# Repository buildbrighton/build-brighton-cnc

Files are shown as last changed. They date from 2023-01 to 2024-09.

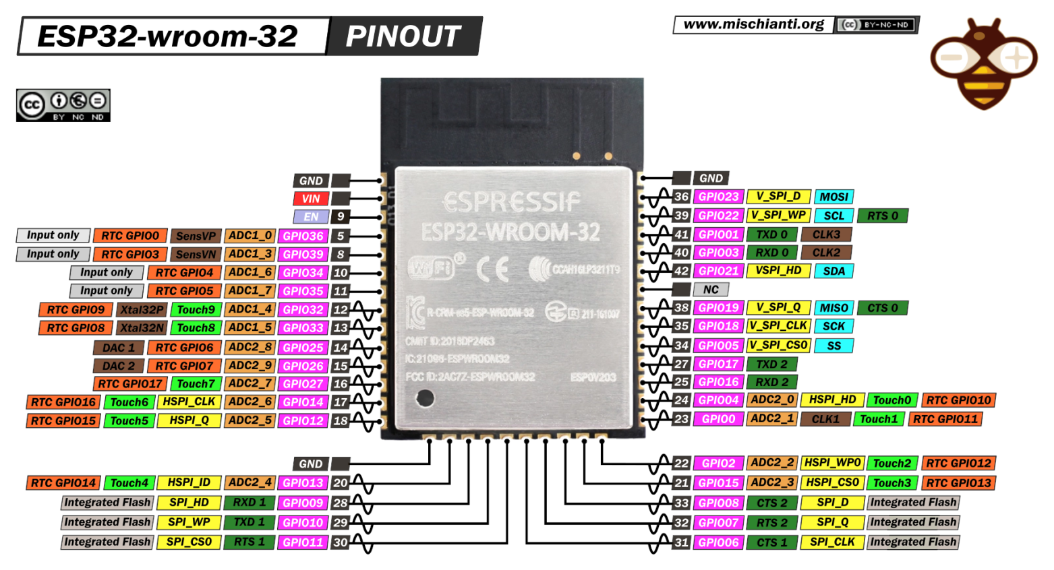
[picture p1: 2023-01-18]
images/ESP32-wroom-32-pinout-mischianti-high-resolution.png

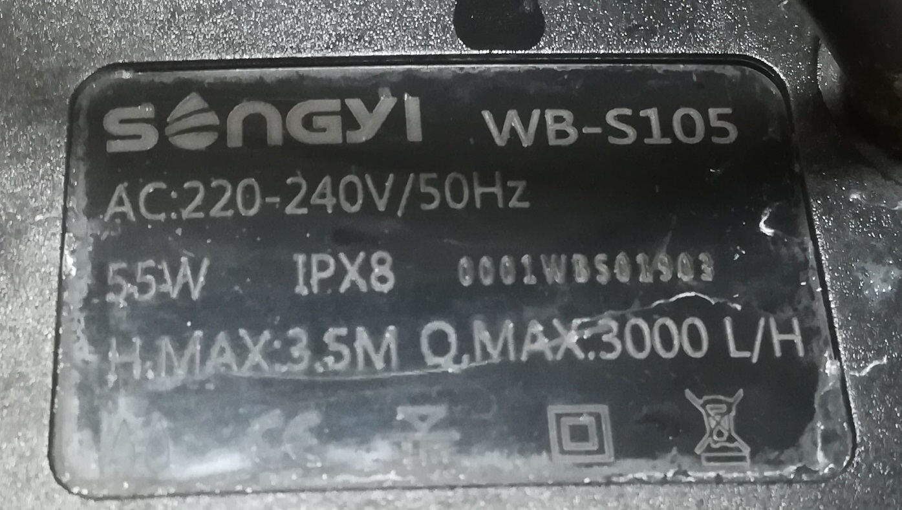
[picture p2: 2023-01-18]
images/water_pump_name_plate.jpg

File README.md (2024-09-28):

# build-brighton-cnc

A repository of code and information about the CNC machine at Build Brighton

You must be inducted to use this machine.

## Machine Description

#### Type

The machine is an ISEL 4433 with a FluidNC controller and a water cooled spindle.

#### Size

The maximum coordinate volume of the machine is 440 x 330 x 160 mm.
The water cooled spindle collides with the door, so the maximum usable depth is 430 mm
The bed is about 300 mm wide.
The X axis is +ve from left to right, Y axis is +ve from front to back, and Z axis is -ve from top to bottom.

#### Spindle

The spindle is rated at 2.2kW and has a speed range of 250 - 24000 rpm.
Speed is controlled by the control board via pwm, start and reverse signals.

#### Spindle Coolant

Coolant for the spindle is stored in a tank under the machine. The pump is located inside the tank. The coolant is tap water and dettol floor cleaner.

#### Control

The control board is an MKS-ESP32. Connection to the controller is either by direct USB or wifi. A PC is setup for use with the machine. It can be controlled directly from a phone or tablet, but the PC is recommended. The PC is dual boot Windows 7 or Ubuntu 16.04 LTS, both of which are out of date and should be upgraded. The PC only has 2GB of ram, which is barely adequate.

## Usage

***DO NOT RUN THE MACHINE WITH THE DOOR OPEN*** Or you will damage yourself.

***DO NOT CUT DIRECTLY ON THE BED*** Or you will damage the bed.

***DO NOT CUT STEEL*** Or you may damage the bearings, ballscrews etc.

***DO NOT DROP TOOLS*** The cutting edges will be damaged and it won't cut well, or at all.

***TOOLS ARE SHARP*** They will slice your skin if handled without care.

***USE A VACUUM IF CUTTING WOOD*** Prefereably, don't cut wood. Use the Carvey for that.

#### Setting up

1. Remove any boxes, equipment or material stored in the machine cabinet. Ensure nothing will get in the way of the moving parts. Don't leave anything in there you down want covered in chips and cutting fluid.

2. Check spindle cooland level and condition. Top up or clean out and replace as required. The level must be at least above the pump, but no more than about 60% full. Make sure the return hose is pointing into the tank and that the tank is covered.

3. Connect the machine, PC, monitor to a power extension cable. Be sure not to cause a trip hazard.

4. Turn on the PC and boot into Linux or Windows. Windows is recommended for now.

5. Connect the water pump to power and check for steady flow of coolant from the return hose.

6. If air cooling is required (recommended), follow procedure for turning on the compressor and run the hose to the air connector on the left front leg.

7. Turn on the machine using the power switch on the right hand side. Release the Emergency Stop button.

8. Connect to the controller. On Windows, this can be done over USB using GRBLPlotter. However, GRBLPlotter is not fully compatible with FluidNC. Alternatively any terminal emulator can connect for a text only interface. FluidNC's web interface is not set up for DNS and itsip address is dynamically allocated, so it must be found using a tool such as Ning (Android) to list all ips on the the network and connecting to each one until the web interface appears. Make sure to connect with `http://` and not `https://`. If anyone knows how to setup a static ip address or configure the DNS, please do.

9. Home all axes using the 'Home All' button next to the jog control, or enter the command `$H`. The machine should gently move into the top left rear corner and back off, one axis at a time.

#### Running a program

1. Upload your gcode to the control board via the web interface. Use a folder with your name to store your files. Alternatively load into GRBLPlotter, etc.

2. Affix you stock material to the bed. For thin sheet material, place a sacrificial block of material under your stock to protect the machine bed. NEVER CUT DIRECTLY ON THE BED. Bar clamps can be used to hold the stock and sacrifical layer to the bed. Bar clamps must have roughly equal height material on both sides of the bolt to function correctly. For thicker and smaller peices, use the clamp/support blocks fixed to the near left corner. The cam grip should be on the right hand side so that its clamping force does not cause it to slide along the T slot. Use shim blocks if the stock doesnt reach the clamp. Make sure that your stock has enough clearance at the edges so as not to cut into the blocks.

3. Change the tool. 
     1. Press the white button on the left hand side. The machine will move the spindle over the tool height probe.
     2. Open the door and use an 18 and 22 mm spanner to remove the collet nut.
     3. Replace the collet with the correct size for your tool. The tool can be up to approx 10% smaller than the collet size and still work.
     4. Insert the collet into the nut *first*, then insert the tool, making sure that the shank of the tool reaches the rear of the collet's gipping surface.
     5. Thread the nut back on to the spindle until finger tight. Use the spanners with *reasonable* force to securely tighten the nut.
     6. **Close the door** and press the *'Start'* button. The machine will move down until the tool touches the tool height probe.
     7. Read the second tool probe Z position. Subtract from 150. Enter the command `G43.1.Z{result}` replacing `{result}` with the value just calcuated. eg, probe return -124.5, value entered is 150 - 124.5 = 25.5
     8. Validate the tool height offset with the command `$#` and check that TLO matches the value entered.

4. Locate the stock. This can be done by eye, or by gently jogging the tool (with the spindle running) into the stock untill it starts cutting. There is also a set of wigglers in the red toolchest in the metal shop that can do the same without cutting into the stock, and is potentially more accurate. Wigglers require an extra tool change. Generally, either the top centre or top near left corner are used for location.

5. Select and zero the work coordinate offset with the commands `G54` and `G92 X0 Y0 Z0`. Each axis can be zeroed independantly after locating for convenience, eg `G92 X0`.

6. If required, open the door and apply cutting fluid to the stock and tool. **Close the door** when done.

6. Press the play button next to your gcode in the web interface, or start sending gcode if using GRBLPlotter or similar.

7. Observe the machine. Do not let it run unattended. You will almost certainly need to adjust feeds and speeds with the override controls, make sure chips are clearing correctly, and that generally everything is ok. The machine should sing with good settings. Bad settings will make it sound like a wood chipper.

8. Press the red *'Stop'* button at any time to hold the program. Press the green *'Start'* button to resume. To stop the program completely use the stop button in the web interface or gcode sender. In an **emergency**, use the *emergency stop* button on the right hand side near the power switch.

9. Your gcode should include a `G28` command at the end to return the machine to the home position. If you stop for any other reason, enter the command `G28` to move the machine back to home and out of the way.

10. When using multiple tools, save each tool operation as a seperate g-code. Repeat steps 3 and 6 through 9 for each tool. When using multiple setups (eg, flipping the stock upside-down, or setting it on its side) repeats steps 2 and  4 through 9 for each setup.

#### Finishing

1. Remove the tool from the collet. Clean chips and cutting fluid from the tool. Put the tool safely back in its protective packaging and return it neatly to where it belongs.

2. Ensure the machine has returned home with `G28`, that the spindle is stopped with `M5`, and that air cooling is turned off with `M9`.

3. Unclamp your work and remove it and any fixturing, like a sacrificial board or clamp shim blocks.

4. Clean out ***all*** the chips, cleanup any cutting fluid and degrease.

5. Turn off the pump, the machine and this PC.

6. Stash whatever machine related things you pulled out of the enclosure back inside and close the door.

7. Carefully roll up the power extension cable and return it.

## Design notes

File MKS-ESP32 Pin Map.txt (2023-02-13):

ESP32 gpio map for MKS-DLC32, plus Expander Board v0.9

GPIO No.	MKS Net			Other			MKS Port	EXP Board	Function
gpio.0		I2C_SDA			BOOTMODE		EXP2.4		SW4			MACRO
gpio.1		TXD				USB
gpio.2		IO2				Blue LED
gpio.3		RXD				USB
gpio.4		I2C_SCL							EXP2.5		SW5			DOOR/INTERLOCK 
gpio.5		LCD_EN							EXP1.3		OC3			FORWARD
gpio.6		Unusable		CLK
gpio.7		Unusable		SD0
gpio.8		Unusable		SD1
gpio.9		Unusable		SD2
gpio.10		Unusable		SD3
gpio.11		Unusable		CMD
gpio.12		SD_DO
gpio.13		SD_DI
gpio.14		SD_SCK
gpio.15		SD_CS
gpio.16		I2S_BCK
gpio.17		I2S_WS
gpio.18		LCD_SCK							EXP2.2		SW2			CYCLE START
gpio.19		LCD_MISO						EXP2.1		SW3			FEED_HOLD
gpio.20		n/c
gpio.21		I2S_DATA
gpio.22		PROBE							J12						PROBE
gpio.23		LCD_MOSI						EXP2.6		SW1			RESET/ESTOP
gpio.24		n/c
gpio.25		LCD_CS							EXP1.7		OC1			PWM/SPEED
gpio.26		LCD_TOUCH_CS					EXP1.5		OC2			REVERSE
gpio.27		LCD_RST							EXP1.4		OC4			FLOOD/AIR
gpio.28		n/c
gpio.29		n/c
gpio.30		n/c
gpio.31		n/c
gpio.32		LC								J7			OC6			AUX1
gpio.33		LCD_RS							EXP1.8		OC5			MIST
gpio.34		Z-								J11						LIMIT_Z
gpio.35		Y-								J10						LIMIT_Y
gpio.36		X-				SENSOR_VP		J9						LIMIT_X
gpio.37		n/c
gpio.38		n/c
gpio.39		SD_DET(n/a)		SENSOR_VN

i2so.0		#STEP_ENABLE
i2so.1		X_STEP
i2so.2		X_DIR
i2so.3		Z_STEP
i2so.4		Z_DIR
i2so.5		Y_STEP
i2so.6		Y_DIR
i2so.7		BEEPER							J4			OC7			AUX2

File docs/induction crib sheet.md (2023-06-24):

### Isel CNC induction crib sheet (draft)

- Main Power - plug, switch, estop
- Cooling pump - power plug, water level, flow rate
- Connectivity - fluidNC, ning, wifi, pc via serial port, gcode senders, GRBL Plot
- Web gui - axis DROs, homing the machine, jog joystick, speed and feed overrides, message window, reseting and clearing faults, command line, supported gcode, running gcode from SD card
- Endstops - no software endstops, pulling the machine off the stops
- Start and Stop physical buttons - stop is feed hold, start is resume
- Changing tools - tool change macro, ER collet operation, height probe
- Available tools, tool wear and breakage
- Spindle behaviour - torque curve, motor heat source
- Feeds and speeds - tool material and diameter, chip loading, deflection, material properties, heat removal
- Clamping work to the bed, sacrificial material, blocks and clamps
- Work coordinate offsets G54-G59
- Door safety - do not run with the door open,
- Cleaning up afterwards - dust, swarf, cutting fluid

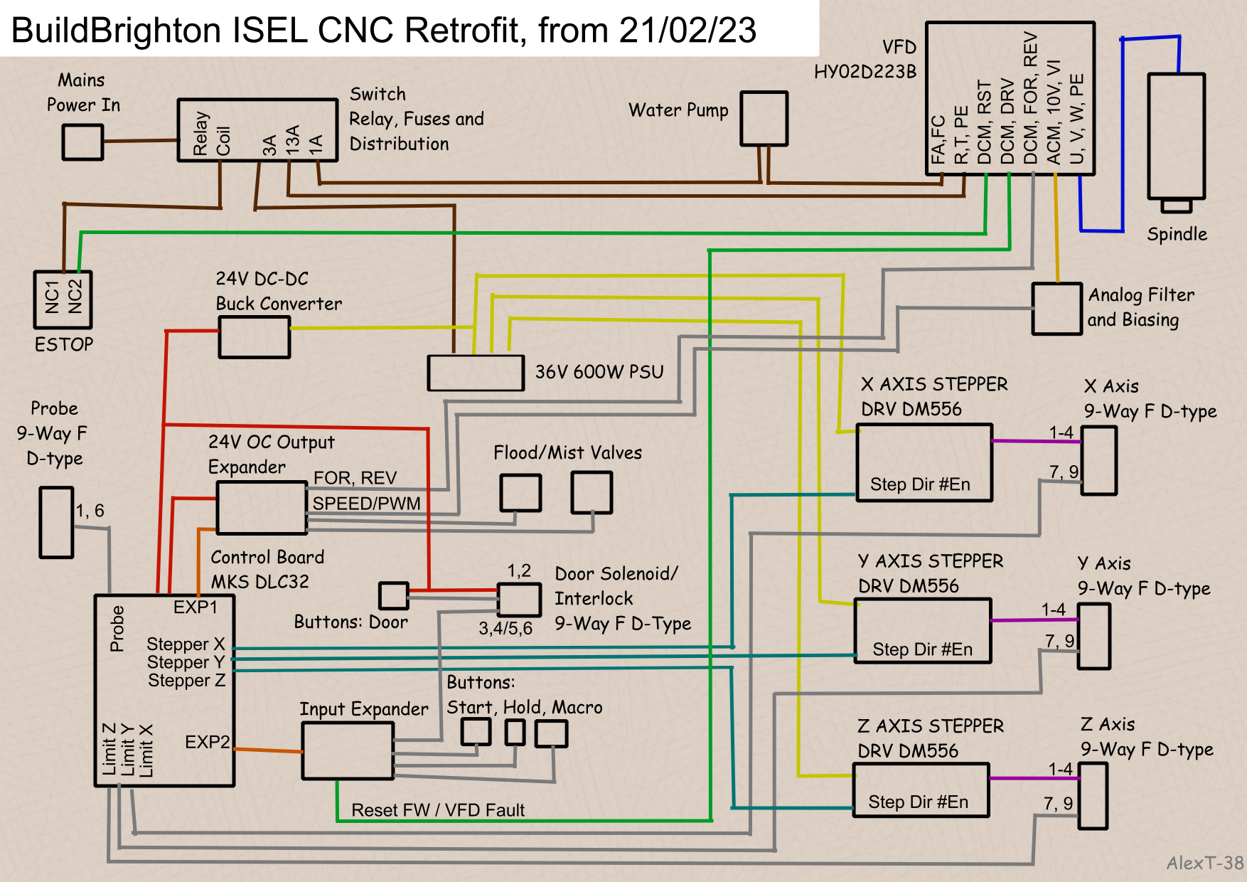
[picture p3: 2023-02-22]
images/refit_schematic_overview.png

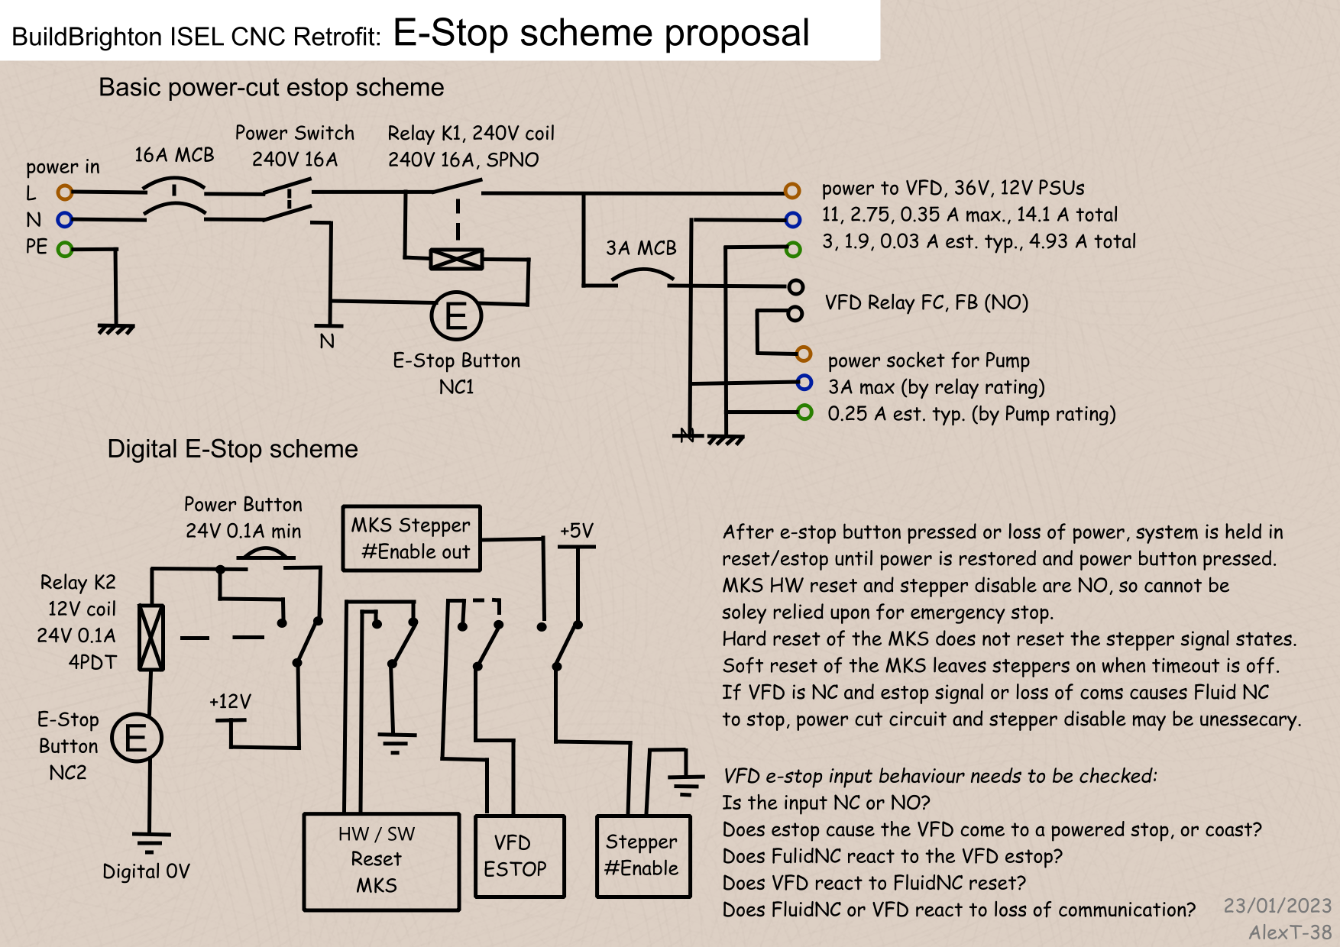
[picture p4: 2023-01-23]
images/cnc_estop_schemes.png

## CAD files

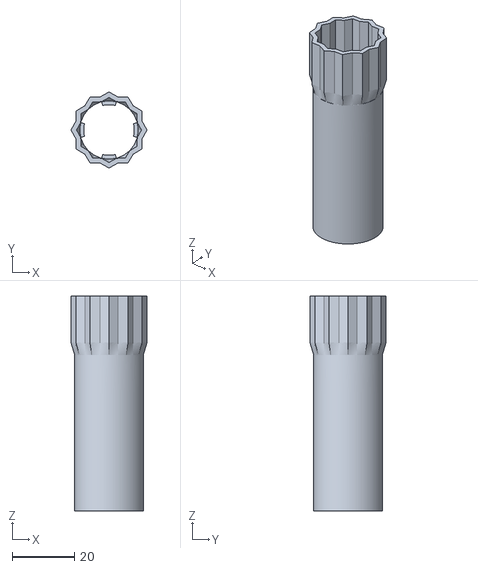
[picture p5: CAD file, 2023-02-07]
hardware/accessories/EAO Series 31 Push Button Accessories v1.stl
24.4 x 24.4 x 69.0

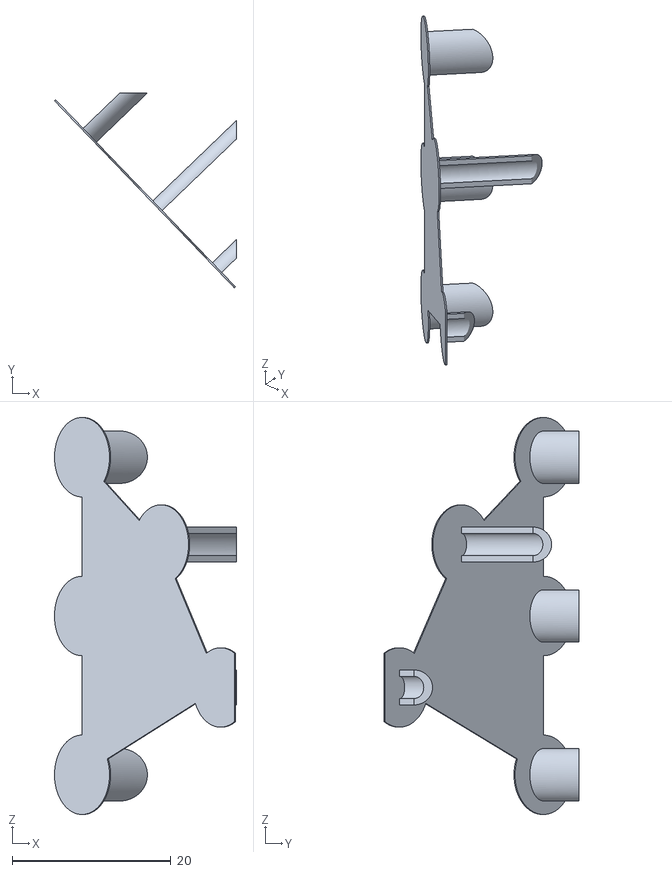
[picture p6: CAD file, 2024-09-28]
hardware/models/Valve Bracket supports.stl
22.9 x 24.5 x 50.0

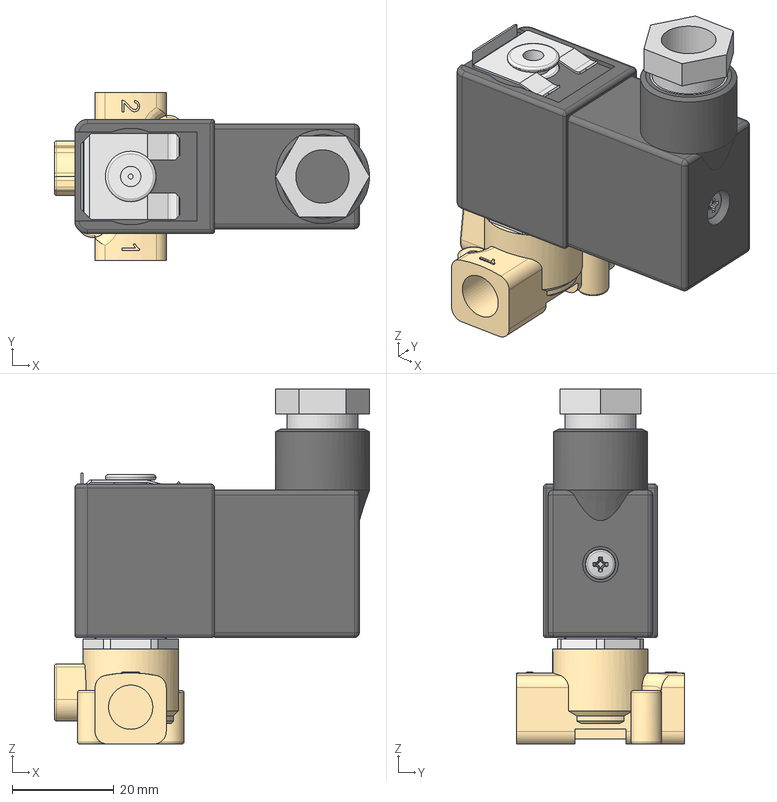
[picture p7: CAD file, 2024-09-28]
hardware/models/ASGO-G356A001.step
62.0 x 33.0 x 69.8 mm
Connector
Solenoid
Valve Body
92005A132_NO THREADS_Steel Pan Head Phillips Screw

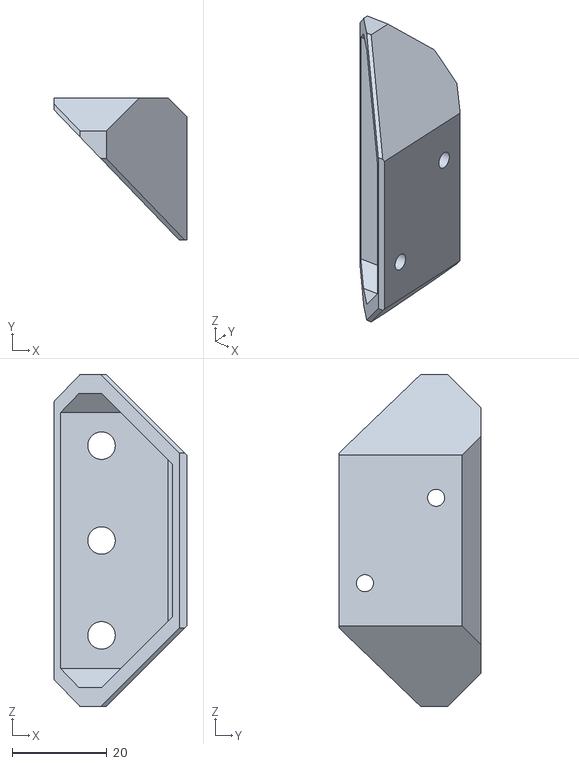
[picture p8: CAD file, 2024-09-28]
hardware/models/Valve Bracket.stl
28.0 x 30.0 x 70.0

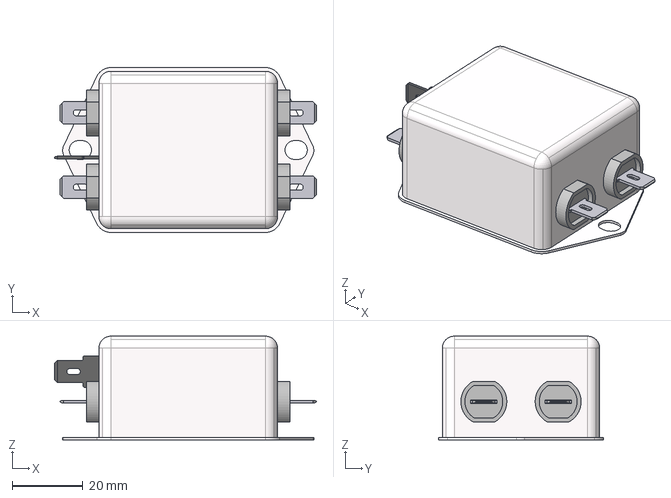
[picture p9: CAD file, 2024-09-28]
hardware/models/fn2060-6-06.stp
74.0 x 46.6 x 29.3 mm

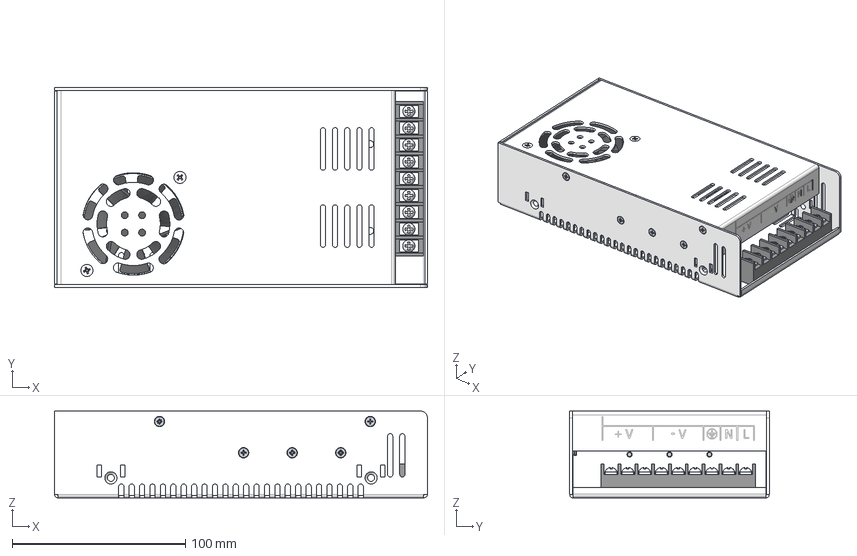
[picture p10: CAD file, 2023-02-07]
hardware/models/Pulse_power_supply_36V_600W.stp
215.0 x 115.0 x 50.0 mm
Основание ИИП
Крышка ИИП
ISO 7046-1 - M3 x 4Z x 12
Кулер 60 х 60
Шайба 4х4х1.3 x 9
Винт M4x6 с полукруглой головкой x 9
Винт М4х12 x 2

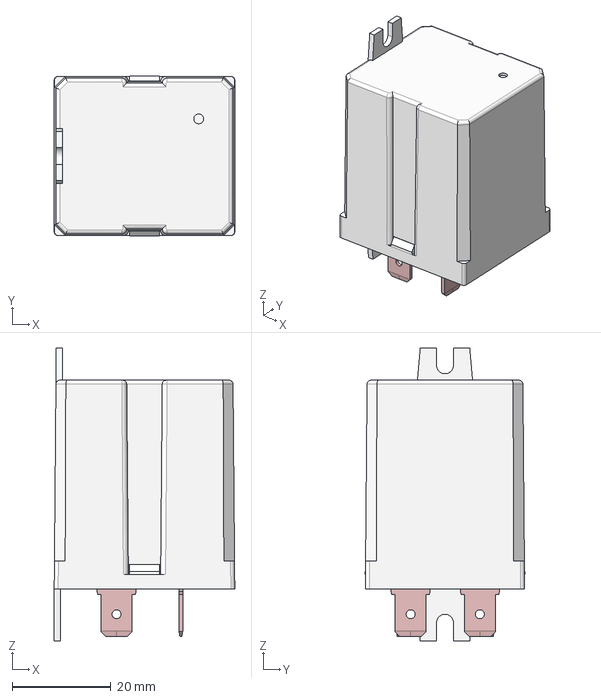
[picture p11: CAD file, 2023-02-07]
hardware/models/6531xxxx0300.stp
36.5 x 32.3 x 59.2 mm

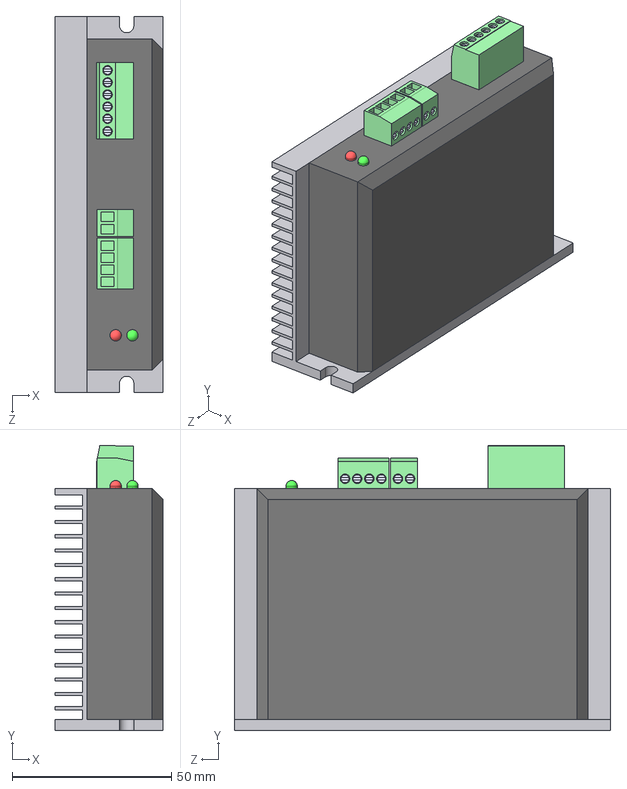
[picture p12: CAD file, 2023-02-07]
hardware/models/Lead Shine DM556.STEP
34.0 x 89.5 x 118.0 mm

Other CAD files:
fusion360/FluidNC Refit Machine Model.f3d

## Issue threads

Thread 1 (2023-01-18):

VFD electrical installation issues.

AlexT-38, 2023-01-18:
Power input cable undersized and wrong type (appears to be 5A 2 core).
Protective Earth not connected to spindle or mains power input.
Spindle loom has PE, but is not connected at the VFD.

Action to take:
1) replace mains power input cable with 3 core flex with current rating >=10A
2) connect VFD PE to spindle loom PE at terminal block below VFD.

AlexT-38, 2023-01-21:
Flex has been upgraded.
Spindle loom and VFD bonded to protective earth.
Will close this issue once the installation has been checked and tested.

Closed 2023-02-10.

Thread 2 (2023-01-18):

VFD is missing opto-isolators for digital outputs

AlexT-38, 2023-01-18:
The VFD's configurable open-collector outputs UPD and DRV do not work because their opto-isolators have not been fitted to its control board.
This is a known issue with Huanyang VFDs since at least 2014.
If these outputs are required, the missing parts can be purchased and soldered onto the board relatively easily.
see: https://www.youtube.com/watch?v=cSjaUhPZzqM

AlexT-38, 2023-02-10:
As we are using FOR/REV/PWM control going forward, we should fit these missing components so that we can use the relay for the cooling pump and the digital OC outputs to signal faults to the controller.

AlexT-38, 2023-02-10:
Parts ordered.

AlexT-38, 2023-03-06:
Fitted and working.

Closed 2023-03-06.

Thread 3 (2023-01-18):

Water pump hose barb is wrong size

AlexT-38, 2023-01-18:
The water pump output has an M20x1.75F thread.
The hose is 10/8mm (OD/ID)
The hose barb thread measures as M19.5x1.5, and fits 5/8" (15.9mm) hoses.
Currently the hose is wedged into the hose barb ID using electrical tape to pad the hose out to 12mm.
The threads catch just enough to stop the barb from simply falling out.

M20x1.75M threaded hose barbs do not appear to exist.
Nor is there any sign of a supplier of accessories for this brand of pump.

A suitable hose barb will have to be printed, or machined if a print isn't up to the job.

Closed 2023-02-10.

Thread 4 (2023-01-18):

VFD Aux Pump does not start.

AlexT-38, 2023-01-18:
The VFD's relay output does not operate when configured as the aux pump output.

With the following parameters set (where non-default),

PD130: 1 - no. of aux pumps
PD052: 25 - output F: aux pump 1

relay is expected to operate on run-start and release 20s after run-stop.

Relay output confirmed working by setting:

PD052: 01 - output F: in run

This setting stops the pumps as soon as the motor has stopped, which in practice is probably sufficient.

AlexT-38, 2023-02-10:
PD135 controls the minimum motor drive voltage below which the pump will stop running (after PD136 seconds).
The default is 95%, which is probably why this wasn't working.

PD138 and 139 appear to provide similar limits based on spindle frequency. However the manual is as clear as muck on the matter, and refers only to "sleep time" for these parameters and PD137, rather than "pump sleep time" for PD135 and PD136.

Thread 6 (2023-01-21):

Spindle collides with door.

AlexT-38, 2023-01-21:
Spindle (specifically the mount) collides with the front panel of the door when the gantry is on the -Y limit switch.
Y-homing is currently configured to use the +Y limit switch.
The -Y limit switch position can be adjusted by loosening the mounting screws and sliding it.
Slack in the wire loom may be the limiting factor on switch placement.

AlexT-38, 2023-03-06:
Not fixed yet, but moved G28 to back left instead of front left (this is also where it homes to). Fusion360 uses G28 to park the machine after completion.

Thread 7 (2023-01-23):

E-Stop implementation

AlexT-38, 2023-01-23:
See [FluidNC E-Stop docs](https://github.com/bdring/FluidNC/wiki/E-Stop-Button) and [onefinitycnc forum post](https://forum.onefinitycnc.com/t/best-way-to-e-stop-spindle-and-vfd/10792).

#### E-Stop requirements
We need to ensure that the machine can be safely stopped in an emergency. This includes machine faults, as well as direct risk to life events.
The method used should fail safe. That is, if any part of the e-stop system fails, estop should be activated.
Loss of power to the control board or spindle should activate the estop.
After loss of power, restoring power should not allow the machine to move until estop condition is reset.
Operation of the door lock/interlock will be considered as a separate issue.

#### Recomendations
FluidNC docs recommend cutting the power.
The onefinity form post on the subject recommends against cutting power to a running VFD, but that if risk assessment requires cutting power, the entire machine should be cut off.

Cutting the power will not stop the machine until it has discharged any energy stored in the VFD, stepper drivers and stepper PSU (although in practice this may happen very quickly).

#### Digital e-stop methods
FluidNC can be reset via gpio, rather than the hardware reset pin.
This will immediately halt the machine and stop the spindle. Steppers will remain energised if the timeout is disabled (which currently it is, to avoid losing position when idle).

The stepper motor enable input is NO(normally open) and must be supplied with current to disable the motors. This isn't ideal because a break in the circuit would prevent the motors from being disabled.

The VFD has an 'estop' signal input. The docs give no detail on how it functions, but presumably it complies with the ISO standards and takes a NC (normally closed) input. Presumably this results in a coasting stop rather than the powered stop that the 'stop' signal would cause.

FluidNC should raise an alarm if the spindle speed falls below target speed, and may also raise an alarm if the VFD reports the estop or stop inputs.

#### Proposed Schemes
One or more of the following schemes should be implemented:
1. estop button de-energises a 240V relay, K1, that cuts power to all parts of the machine
2. estop button directly breaks FluidNC 'reset' signal, controlled stop of machine
3. estop button directly breaks VFD 'stop' signal, FluidNC responds via comms, controlled stop of machine
4. estop button directly breaks VFD 'estop' signal, FluidNC responds via comms, controlled stop of stages, spindle coasts to a stop
5. estop button de-energises a 12V relay, K2, which breaks 'reset' and 'stop'/'estop' signal to FluidNC and VFD
6. K2 also overrides stepper #Enable signal and de-energises steppers
7. K2 also latches off, requiring the Power Button to be pressed after power is supplied to reset K2
8. K2 makes MKS reset pin input instead of breaking FluidNC soft reset.

#### Comments
The exact behaviour of FluidNC and the VFD with regards to stop signals and loss of communication needs to be examined before a scheme can be settled on.

AlexT-38, 2023-01-27:
FluidNC does not stop when VFD comms lost, despite setting an alarm.
VFD does not stop when comms lost. This is not ideal.

Spindle shuts down within 0.5s of loss of power. Not sure if it coasts.

FluidNC 'reset' input and VFD 'estop' functions not yet tested.

AlexT-38, 2023-02-10:
The VFD reports an under voltage fault when power is cut.
The VFD can also be configured to raise faults for over temperature and over torque conditions.
The fault state of the VFD can be signalled using one of its digital outputs. It is not clear if its operation is NC or NO.
As FluidNC does not have a 'wait for spindle' input, we should use the general fault signal to stop all motion.

The three FluidNC inputs we can use for this are _Feed Hold_, _Reset_ and _Saftey Door_.

_Reset_ causes immediate stop of motion and disabling of axis motors. This would be the simplest implementation.

_Feed Hold_ needs to be tested, but it might not respond immediately depending on how it's implemented. If it interrupts the current motion then it would be useful in case of an over torque or other VFD only fault. Estop would still need to be wired to the _Reset_ signal so that a commanded estop causes immediate stop of motion. However, the feed hold button input would have to be wired in series with the fault signal.

_Safety Door_ does not stop motion, but interrupts the current program and moves to the parking position. Probably not what we want, but could be suitable for faults that cause the VFD to stop the spindle. Using this input would be simpler than _Feed Hold_ unless we also want to implement the door interlock.

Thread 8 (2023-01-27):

VFD comms lost after starting spindle

AlexT-38, 2023-01-27:
FluidNC loses communications with the VFD after starting the spindle by issuing M3 command.
Communications cannot be restored until FluidNC has been restarted.
Spindle can _ONLY_ be stopped by the button on the front panel.
Data cable is screened and was routed far from the spindle loom, so unlikely to be a noise issue.
All other comms seem to work (eg fetch min and max rpm) prior to loss of comms.

Suspect the auto arbitration on the DMX board? Would an extra line to control TX/#RX enable work?

AlexT-38, 2023-01-27:
Baud rate is 9600, VFD freqeuency is 8000Hz.
Those are awfully close, so it could yet be interference.

Suggest:
1. Increasing VFD frequency,
2. decreasing baud rate,
3. replacing spindle loom with screened cable.

We've got some screened 6-core that might be suitable.

AlexT-38, 2023-02-10:
Screening the spindle loom improved the problem, but the connection was still unreliable.
After trying out a FOR/REV/PWM interface, no communication with the spindle has been possible.
No obvious problem was found with either the configuration or the hardware layer. Signal was traced from ESP's gpio all the way to the digital output of the VFD's RS485 transciever. The VFD would only respond intermittently, but while the signal was seen on the bus, it was not observed on the RX pin on the control board. This may have been down to having an inadequate scope.
Regardless, going forward we will use FOR/REV/PWM control rather than sinking more time into this.

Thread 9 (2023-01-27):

FluidNC soft limits cause motors to disable.

AlexT-38, 2023-01-27:
Soft limits are intended to prevent motion outside of the machine work volume without colliding with the hard limit switches, thus preventing loss of position.
However, FluidNC disables the stepper motors when an out of range command is received, causing immediate loss of position, defeating the purpose of the soft limits.

AlexT-38, 2023-01-28:
See https://github.com/bdring/FluidNC/issues/471
This is a known issue that may be fixed sometime in the future.
In the mean time soft limits should be disabled, since they provide no benefit over hard limits.

AlexT-38, 2023-02-10:
Closing this, no further action to be taken.

Closed 2023-02-10.

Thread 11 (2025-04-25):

VFD back powers MKS board via switch input pullups

AlexT-38, 2025-04-25:
With power disconnected from the MKS DLC32 control board, the VFD's internal pullups for switch inputs FOR and REV are providing power to the +24v rail.

Power is transfered from the switch outputs to the 24v rail via 1N4148 diodes used for inductive / EMI clamping.

Suggested solution:
Fit a 1N4001 diode to the 24v power input.

This would limit the maximum current output to 1A.
Only the AIR/MIST outputs use 24v power. The valve coils are rated at 5W and draw aprox 250mA each. this is well within the 1A limit.

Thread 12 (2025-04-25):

24v supply drops to 12v when AIR valve active.

AlexT-38, 2025-04-25:
AIR valve operation was observed to be unreliable, either delayed or not activating at all.

Coil voltage is rated at 24v.
Voltage supplied to the coil was measured at 12v.
Supply voltage is 24v when the coil is not energised.

Possible causes:

- DC-DC convertor is not working corectly
- Output fet is not switching on fully.

AlexT-38, 2025-04-25:
DC-DC is holding 24v when AIR is enabled.

BS170 maximum gate threshold is 3V, but at that voltage Id is between 50 and 150mA. This isn't enough for the solenoid, which requires 250mA.

This also means that 1.2W is being disspated by the FET, which is 50% higher than rated Pd of 830mW.

Suggested solutions:

- Find a fet with the same package and Id max, but with 4.4v compatible input.
- Add a BJT to drive the gate from 24v.

AlexT-38, 2025-04-25:
Recommended replacement part:
TN0604N3 - Vds 40V Id(cont) 0.7A Vg(th) 1.6

At Vg = 3.0, Id max is approx 300mA at 125°C and approx 600mA at 25°C

https://uk.farnell.com/microchip/tn0604n3-g/d-mosfet-n-ch-0-7a-40v-to-92-3/dp/2851581

AlexT-38, 2025-04-29:
TN0604 was not readily available, so I've replaced them with BC337 for the coolant channels only. I've replaced the link wires with 270 ohm resistors to reduce the base current to around 7mA. BC337 gain is around 60, giving us 400mA output current.

I also spotted and fixed a couple of errors.
1. Gound on the ribbon cable was not connected. This may have been deliberate to avoid ground loops, but it could cause problems if the 24v input is disconnected.
2. The pwm output had its indicator led rewired to run on 5v, since the analog voltage in the vfd is 10v, so the led was always forward biased. However it was actually connected to flood/air control gpio.

The circuit diagram and pcb layout need to be updated to reflect these changes.

AlexT-38, 2025-05-01:
Tested and working.

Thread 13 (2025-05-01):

FluidNC is crashing repeatedly.

AlexT-38, 2025-05-01:
FluidNC is crashing semi randomly, but mostly after starting the spindle or enabling air coolant.

It is currently not possible to use the machine.

Given that it's been working fine for some time with crashes only occuring rarely, it's possible that changes to the output expansion board for issue #12 may have something to do with it.

I'm going to upgrade the firmware (from 3.6 to 3.9) to see if that has any effect before checking for electrical faults.

This upgrade was required anway to fix TLO offset being lost when stopping a program.

AlexT-38, 2025-05-01:
The 24V DC-DC convertor is not working.

AlexT-38, 2025-05-01:
Works on the bench with no load.

AlexT-38, 2025-05-01:
Firmware upgrade compleed successfuly, but did not resolve the issue.

However, more info is available from the serial monitor:
```

[TLO:1.298]
Grbl 3.9 [FluidNC v3.9.6 (wifi) '$' for help]
[MSG:ERR: reset_pin is active at startup]
Grbl 3.9 [FluidNC v3.9.6 (wifi) '$' for help]
[MSG:ERR: reset_pin is active at startup]
Grbl 3.9 [FluidNC v3.9.6 (wifi) '$' for help]
[MSG:ERR: reset_pin is active at startup]
Grbl 3.9 [FluidNC v3.9.6 (wifi) '$' for help]
[MSG:ERR: reset_pin is active at startup]
Grbl 3.9 [FluidNC v3.9.6 (wifi) '$' for help]
[MSG:ERR: reset_pin is active at startup]
Grbl 3.9 [FluidNC v3.9.6 (wifi) '$' for help]
[MSG:ERR: reset_pin is active at startup]
[MSG:INFO: ALARM: Control Pin Initially On]
ALARM:11
ALARM:11
[MSG:INFO: ALARM: Control Pin Initially On]
ALARM:11
ALARM:11
[MSG:INFO: ALARM: Control Pin Initially On]
ALARM:11
ALARM:11
[MSG:INFO: ALARM: Control Pin Initially On]
ALARM:11
ALARM:11
[MSG:INFO: ALARM: Control Pin Initially On]
ALARM:11
ALARM:11
Grbl 3.9 [FluidNC v3.9.6 (wifi) '$' for help]
Grbl 3.9 [FluidNC v3.9.6 (wifi) '$' for help]
[MSG:INFO: websocket auto report interval set to 300 ms]
[TLO:1.298]
[GC:G0 G54 G17 G21 G90 G94 M3 M9 T0 F0 S0]
[MSG:INFO: websocket auto report interval set to 300 ms]
[GC:G0 G54 G17 G21 G90 G94 M3 M9 T0 F0 S0]

```

AlexT-38, 2025-05-01:
Connecting Spindle FOR or REV to Output Board FOR, REV or AIR causes a reset when those signals are active.
Connecting Spindle FOR or REV to Output Board RPM does not.

Since FOR/REV and AIR outputs have different switching devices (BS170 vs BC337), it's unlikely to be an issue with with those devices.

The only difference between RPM and FOR/REV/AIR is that its indicator LED is driven from 5V not 24V.

I'm going to try disconnecting the LEDs from FOR/REV.

AlexT-38, 2025-05-02:
That did nothing. I'm now checking the VFD.

Disconnecting the FOR wire from the terminal block, no reset occurs when activaing the spindle, so probably not a fault with the cable.

The VFD's logic pullups are 24v. The p.d. between FOR signal wire and FOR input terminal with FOR output active is 24v, so ground connection appears good.

Measuring the current I see 0.09A briefly before the controller resets.

I setup a trim pot to increase the effective pullup resistance so that I could check to see if it tipped at some critical current level, but the 24V DC-DC convertor has failed.

I'm going to try the 12V external supply to power the MKS DLC32.

FOR still causes reset. Seting up the trim pot again...

0.02mA ok
0.03mA ok
0.04mA ok
0.05mA ok
0.06mA ok
0.07mA ok
...
0.20mA ok

0.25mA - 0.80mA not ok.

Trip point is not consistant.

Next thing to do is isolate the vfd from the control board and repeat this test with the trimp pot connected dirctly to the output (with some minimal inline resistor for a max of ~20mA), and measure the voltage on the output.

AlexT-38, 2025-05-02:
Rather than doing a deep dive into exactly what is causing the problem, I'm going to make the following changes:

1) replace the DC-DC convertor with a dedicated 24V 2A PSU to provide power for the control board and solenoid valves.
2) opto-isolate the spindle control outputs.

AlexT-38, 2025-05-20:
I've replaced the mosfets on the ouptut board with opto isolators.
FluidNC then started giving me errors because the RESET pin was active at startup.
RESET was connected to the VFD's UPF output.
RESET has been disconnected and now FluidNC is working correctly.

There's no sign of trouble with the DC-DC convertor, so I haven't swapped that for a dedicated supply yet.

VFD speed control is no longer working correctly.
The PWM signal is filtered with a 10k Ohm/ 10uF RC filter, and is pulled up to 10V by a 470 Ohm resistor, requiring 21mA to pull the signal down to 0V.
The optoisolator's input current is 6mA, and its CTR is 130% to 260%.
Shorting the output directly to 10V, the measured current is 21mA.
With the output open, and with speed set to either 10% or 0%, there's no consitant voltage drop betwen signal and 0V or 10V, always readng about 0.2V. This is not expected. With output set to 100%, there should be a approx 10V drop between 10V and and output.

I'll increase the pullup resistor to 1k, which should reduce the current required for 100% on to about 9mA and allow full speed range again.

AlexT-38, 2025-05-20:
1.2K gets us to 20000rpm, 0.744V.
I'll have to look in to changing the calibration in the VFD, if thats possible.

The relevant settings are:
| Setting | Description | Value |
| -- | -- |-- |
| PD070 | Analog Input Mode | 1 : 0-5V |
| PD073 | Lower Analog Freq. | 402 |
| PD075 | Low Freq. Bias Dir. | 0|
| PD072 | Higher Analog Freq. | 4|
| PD074 | Higher Freq. Bias Dir. | 0|
| PD076 | Analog Neg. Bias Rev. | 0|

Why was 0-5V selected?

Increasing PD073 by 7.4% (0.744V/10V) to 432 was not able to achieve full speed, about 22k rpm.
Increasing to about 440 gets us 23300 rpm, but no higher, no matter the setting.
Minimum speed is also wrong.

Let's switch back to 0-10V input, set the FluidNC mapping to 0.5%=240 100%=23300, and he min/max frequencies to 400 and 0, and map the voltages and actual speeds to the demand speed.

| Speed Setting | VI (V) | Speed Actual |
|-|-|-|
|23300| 0.744 | 22275 |
|12000| 2.878 | 17040 |
|6000| 4.36 | 13375 |
|3000| 5.12 | 11496|
|1500| 5.55 | 10440 |
|240| 6.28 | 8660|
|0|6.35 | 8475 |
|disconnected| 6.35 | 8475|

In this disconncted state, Vpullup is 0.378 = 315uA.

Disconnecting VI, VI is 0V and speed is 24000rpm. Vpullup is 0V

Connecting VI to 10V via 1.2K, VI is 9.32V, Vpullup = 0.566 = 471uA

Again, via 10K, VI is 6.6V, Vpullup is 3.28V = 328uA

So VI appears to be a relatively low impedance input, around 20kOhm.

What happens if we connect the opt directly between 10V and VI, swapping min/max frequencies PD072/73?

That kinda works, but with very non linear control, with S240 giving 4660rpm and S12000 giving 23475rpm.

Can we use the VFD's built in filtering?

PD071, Analog Filter 0-50, default 20, currently 20. Set to 50.

Nope, S240 is still 4660rpm.

So, put the 10k and 10uf back in, but replace the pullup with the opto output, and set the voltage range back to 0-5V.

Nope. S12000 is still full speed. This is suggesting that the pulldown is a constant current type, not a simple resistor.

Changing fluidNC's speed mapping to a simple 0%:0 66.6%:24000

So, put the 10uF cap and  10k limiting resistor, set the range to 0-5V. We should now have 0-6.6V, more or less linear.

No change.

I give up for now.

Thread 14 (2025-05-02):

GPIO0 causes issues when used as an external input.

AlexT-38, 2025-05-02:
This wasn't documented at the time this problem was first noted.
I'm documenting it now because the firmware has been updated and this issue may have been resolved.

The original switch input assignments didn't function as intended.
The MACRO button was moved from GPIO0 to GPIO4, and the DOOR_SAFETY input was disabled.
The input assigned to RESET has also been left unused, but this is a separate issue.

From config_frp.yaml:

```
#gpio.0:high //gpio.0 does not seem to work.
#sometimes, fluidnc will spam "MSG:INFO: Check door" and will not funcion until the door input is closed
#sometimes, having the door input closed will prevent fluidnc from booting at all.
# door/inertlock will be disabled until this is fully understood.
safety_door_pin: NO_PIN
reset_pin: gpio.23:low
feed_hold_pin: gpio.19:high
cycle_start_pin: gpio.18:low
macro0_pin: gpio.4:low
```

GPIO_0, and several others, have special functions.

From the ESP32 datasheet:

```
Table 3-1. Default Configuration of Strapping Pins
Strapping Pin | Default Configuration | Bit Value
GPIO0         | Pull-up               | 1
GPIO2         | Pull-down             | 0
MTDI          | Pull-down             | 0
MTDO          | Pull-up               | 1
GPIO5         | Pull-up               | 1
```

GPIO5 is used as an output.
GPIO2 isn't used at all.

GPIO0 and 2 are both pulled low by the USB interface when DTR is low and RTS is high.

GPIO0 puts the controller into a different boot mode if both it and GPIO2 are low.

This is a problem for the door safety input, but shouldn't be for the MACRO button.

So why was MACRO moved onto GPIO4?

Once Issue #13 is resolved, we should revisit this and check if we can move MACRO back onto GPIO0.

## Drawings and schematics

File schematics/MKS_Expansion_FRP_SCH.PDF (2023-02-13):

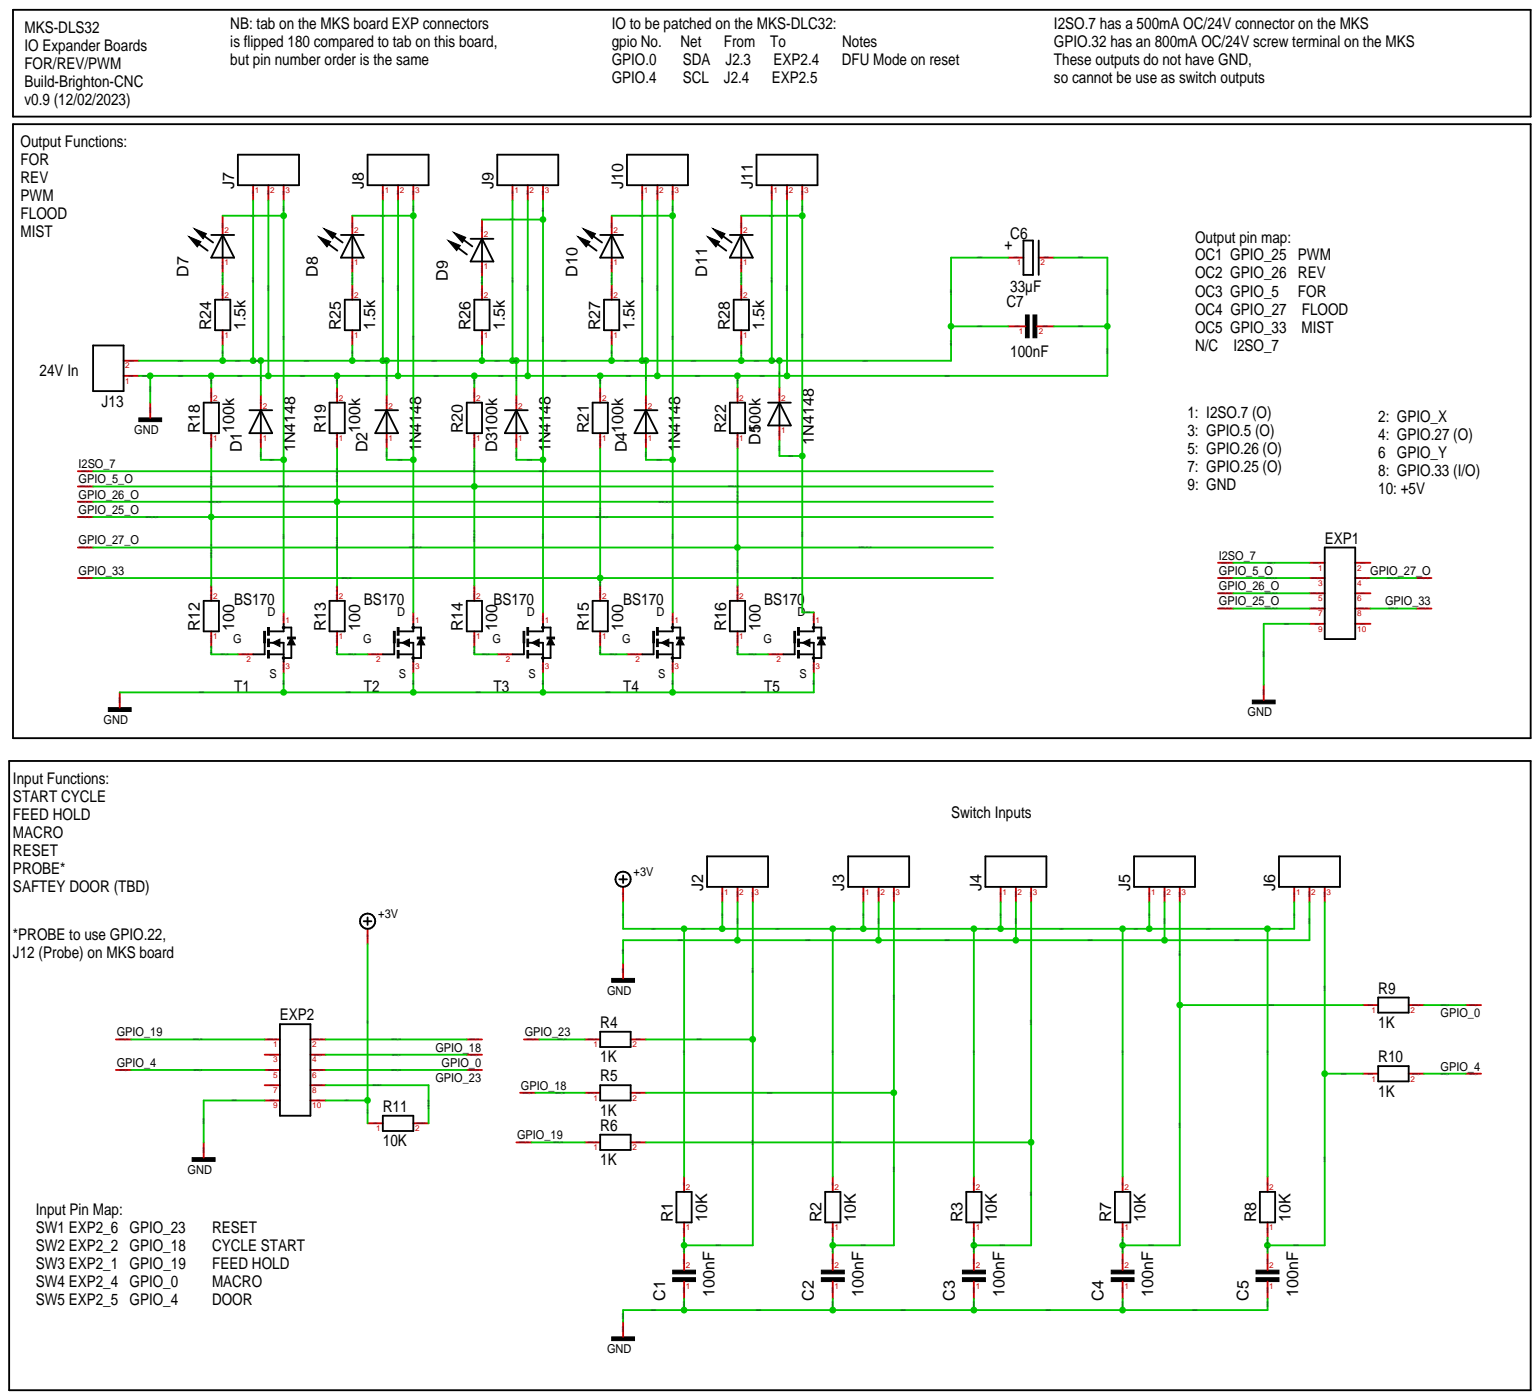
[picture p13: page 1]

NB: tab on the MKS board EXP connectors
is flipped 180 compared to tab on this board,
but pin number order is the same

IO to be patched on the MKS-DLC32:

I2SO.7 has a 500mA OC/24V connector on the MKS
GPIO.32 has an 800mA OC/24V screw terminal on the MKS
These outputs do not have GND,

*PROBE to use GPIO.22,
J12 (Probe) on MKS board

GND | GND | | GND | | GND

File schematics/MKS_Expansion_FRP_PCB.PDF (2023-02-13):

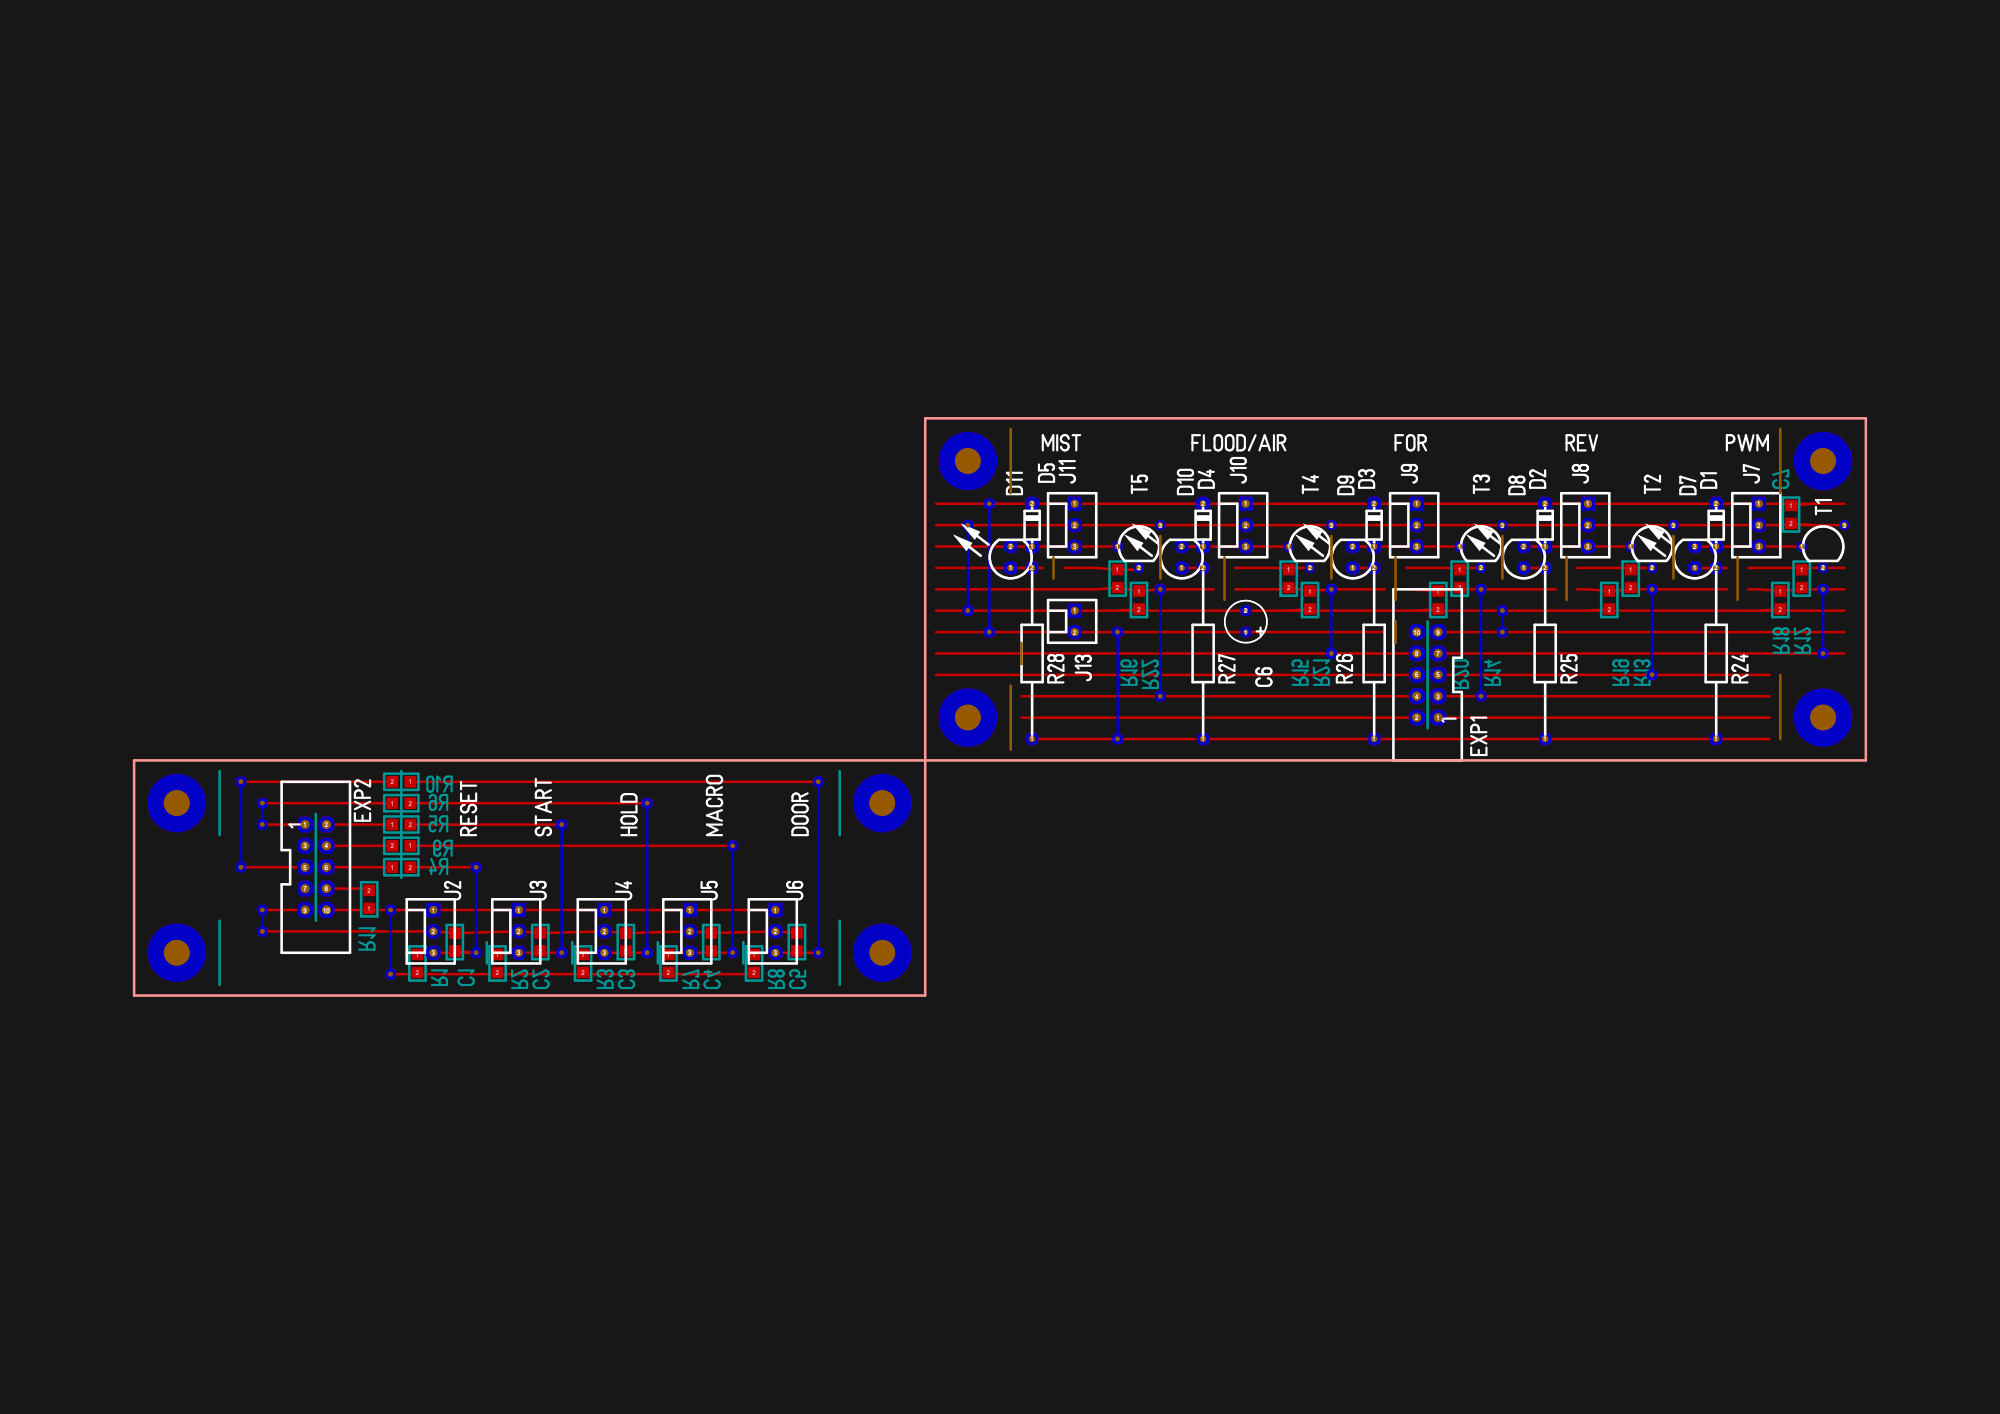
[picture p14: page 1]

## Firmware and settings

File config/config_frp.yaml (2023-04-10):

board: MKS DLC32 2.0
name: MKS DLC32 XYZ
meta: FOR/REV/PWM v0.9 (13/02/2023)
stepping:
  engine: I2S_stream
  idle_ms: 255
  pulse_us: 4
  dir_delay_us: 5
  disable_delay_us: 0
  segments: 6
axes:
  shared_stepper_disable_pin: I2SO.0
  x:
    steps_per_mm: 1280.000
    max_rate_mm_per_min: 2500.000
    acceleration_mm_per_sec2: 100.000
    max_travel_mm: 341.000
    soft_limits: false
    homing:
      cycle: 2
      allow_single_axis: true
      positive_direction: false
      mpos_mm: 0.000
      feed_mm_per_min: 100.000
      seek_mm_per_min: 1000.000
      settle_ms: 500
      seek_scaler: 1.100
      feed_scaler: 1.100
    motor0:
      limit_all_pin: gpio.36
      hard_limits: true
      pulloff_mm: 0.5000
      standard_stepper:
        step_pin: I2SO.1
        direction_pin: I2SO.2
  y:
    steps_per_mm: 1280.000
    max_rate_mm_per_min: 2500.000
    acceleration_mm_per_sec2: 100.000
    max_travel_mm: 430.000
    soft_limits: false
    homing:
      cycle: 3
      allow_single_axis: true
      positive_direction: true
      mpos_mm: 435.000
      feed_mm_per_min: 100.000
      seek_mm_per_min: 1000.000
      settle_ms: 500
      seek_scaler: 1.100
      feed_scaler: 1.100
    motor0:
      limit_all_pin: gpio.35
      hard_limits: true
      pulloff_mm: 0.5000
      standard_stepper:
        step_pin: I2SO.5
        direction_pin: I2SO.6:low
  z:
    steps_per_mm: 1280.000
    max_rate_mm_per_min: 2500.000
    acceleration_mm_per_sec2: 100.000
    max_travel_mm: 163.000
    soft_limits: false
    homing:
      cycle: 1
      allow_single_axis: true
      positive_direction: true
      mpos_mm: 0.000
      feed_mm_per_min: 100.000
      seek_mm_per_min: 1000.000
      settle_ms: 500
      seek_scaler: 1.100
      feed_scaler: 1.100
    motor0:
      limit_all_pin: gpio.34
      hard_limits: true
      pulloff_mm: 0.5000
      standard_stepper:
        step_pin: I2SO.3
        direction_pin: I2SO.4
kinematics:
  Cartesian:
i2so:
  bck_pin: gpio.16
  data_pin: gpio.21
  ws_pin: gpio.17
spi:
  miso_pin: gpio.12
  mosi_pin: gpio.13
  sck_pin: gpio.14
sdcard:
  cs_pin: gpio.15
  card_detect_pin: gpio.39
control:
#gpio.0:high //gpio.0 does not seem to work.
#sometimes, fluidnc will spam "MSG:INFO: Ceck door" and will not funcion until the door input is closed
#sometimes, having te door input closed wil prevent fluidnc from booting at all.
# door/inerlock will be disabled unil this is fully understood.
#reset pin should be active high, but stupid chinese vfd uses NO output.
  safety_door_pin: NO_PIN
  reset_pin: gpio.23:low
  feed_hold_pin: gpio.19:high
  cycle_start_pin: gpio.18:low
  macro0_pin: gpio.4:low
coolant:
  flood_pin: gpio.27
  mist_pin: gpio.33
  delay_ms: 500
probe:
  pin: gpio.22
  check_mode_start: true
macros:
  startup_line0: 
  startup_line1:
#HOME: retract, stop and move to location G30, probe z-height. Tool length offset is probe result minus probe position, which is -150mm (relative to spindle nose minus 20mm)
  macro0: G53 G0Z0 & M9 M5 & G30 & M0 & G53 G38.2 Z-160 F200 & G53 G38.4 Z0 F10 & G53 G0 Z0
  macro1:
  macro2: 
  macro3: 
start:
  must_home: false
  deactivate_parking: false
  check_limits: false
user_outputs:
#gpio.32 (LC/Spindle) J7 800mA open collector output on the MKS-DLC32
  analog0_pin: gpio.32
  analog0_hz: 5000
#i2so.7 (BEEPER) J4 500mA open collector output on the MKS-DLC32
  digital0_pin: I2SO.7
arc_tolerance_mm: 0.002
junction_deviation_mm: 0.010
verbose_errors: false
report_inches: false
enable_parking_override_control: false
use_line_numbers: false
planner_blocks: 16
10V:
  forward_pin: gpio.5:low
  reverse_pin: gpio.26:high
  pwm_hz: 5000
#vfd programed to invert signal so that an open circuit sets zero speed
  output_pin: gpio.25
  disable_with_s0: false
  s0_with_disable: true
  spinup_ms: 15000
  spindown_ms: 15000
  tool_num: 0
  speed_map: 0=0.000% 240=23.5% 24000=100.000%
  off_on_alarm: true
  

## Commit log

2022-05-04 Add reverse engineered schematic for the original control board
2023-01-17 Add DLC32 schematic
2023-01-24 Create MKS_Expansion.T3001
    Added schematic for an IO breakout board providing 5 inputs and 4 outputs.
2023-01-24 Updated config.yaml, added config_io.yaml
    probe pin set gpio.22 as per MKS schematic
    home seek speed set to 1000mm/min for all axes
    added macro to retract, stop and park (G28)
    config_io.yaml:
    added pin configuration for button/relay expansion board
2023-01-24 Updated IO_expander schematic
    swapped some pins for easier routing
    added pdf printout of schematic
2023-01-25 Added expansion board layouts.
    Layouts for strip board.
    Moved GPIO.32 to EXP2.4 to facilitate routing.
2023-01-26 Updated IO Expander
    Swapped RS458 TXD with relay output to make expander board layout simpler.
    Updated config_io.yaml to match new pin assignments.
2023-01-27 Updated configs
    Set max_travel correct for each axis.
    Reduced max speed from 5000 to 1000mm/min
    Increased acceleration 50 to 100 mm/s2
    Reduced pull off from 1.0 to 0.5mm
    Decreased minimum RPM from 6000 to 240
    changed pin allocation to suit expansion board
    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
2023-02-02 Updated schematics for rs485 io
    Added new schematic for expansion board with built in RS485, complete with direction input.
    Added pin assignment table.
    Added new config for the above new expansion board.
2023-02-07 updated config for tristate rs485, added 3d models, added relay board
    config_io2.yaml updated for the latest expansion board with built in RS485 and tristate control
    Expansion board circuit and pcb layout updated to include on board RS485 with tristate control
    Added relay board and milling program
    Added 3d models of system components for layout model
    [6531xxxx0300.stp, EAO Series 31 Push Button Accessories v1.stl, Lead Shine DM556.STEP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]
2023-02-13 Updated IO Expander
    Latest version provides FOR/REV/PWM and MIST/FLOOD open drain outputs.
    Updated pin map for new expansion boards.
    Added new config file config_frp.yaml for new expansion boards.
    Removed duplicate MKS_Expansion boards.
    Removed out dated configs.
    Removed unused 3D models.
    [6531xxxx0300.stp]
2023-02-22 updated config and overview schematic
    gpio.0 did not behave nicely and will not be used for now
    corrected active levels for some i/o pins
    [config_frp.yaml]
2023-04-10 Update config_frp.yaml
    Disabled safety door pin and reassigned macro to that pin due to boot problems
    Spindle Speed Map set, partly with speed_map and partly with VFD params.
    Tool Height Probe Macro working, TLO must be calculated and entered manually
    [config_frp.yaml]
2023-04-12 Fusion360 tools library, machine model and post processor
    Fusion360 tool library for all CNC tools currently in the white box, plus a handful of sharp tools in the milling toolbox. Shaft shapes aren't set up correctly yet.
    Machine definition and model for Fusion360.
    Post processor for FluidNC. Derived from GRBL post.
    [FluidNC Refit Machine Model.f3d]
2024-09-28 Updated models
    [ASGO-G356A001.step, Valve Bracket supports.stl, Valve Bracket.stl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]
